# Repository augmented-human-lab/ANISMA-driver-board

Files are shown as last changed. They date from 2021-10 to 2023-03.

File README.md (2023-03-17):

[ANISMA Main Repository](https://github.com/augmented-human-lab/ANISMA) 
* [ANISMA Software](https://github.com/augmented-human-lab/ANISMA-software)
* [ANISMA Controller Board](https://github.com/augmented-human-lab/ANISMA-controller-board)
* **ANISMA Driver Board** <-- You are here!

# ANISMA Driver Board

This repository provides the Eagle Project files for the ANISMA Driver Board

The Driver Board connects to an Arduino Uno as controller board. They support eight output pins that are fully controlled and can be extended by adding more Driver Boards to an I2C bus system. We use a PCA9685 16-channel LED controller in combination with four MAX14874 dual-channel push-pull drivers in order to control the current flow using pulse-width-modulation (PWM) and dynamically set the polarity (VCC, GND, HIGH-Z) for each output pin. 

# How to get the board

Using the following link you can get direct access to the Gerber files and Bill of Materials (BOM): 
https://www.pcbway.com/project/shareproject/ANISMA_Driver_Board_3e5c784f.html

If you want you can purchase the board directly including assembly via PCBWay.

<a href="https://www.pcbway.com/project/shareproject/ANISMA_Driver_Board_3e5c784f.html">PCB from PCBWay</a>

# Wiring

Wire the ANISMA Controller Board with the Arduino Uno as follows: 

| Arduino Uno | ANISMA Controller Board | Power Supply (9V Battery) |
|---|---|---|
| SCL | SCL | |
| SDA | SDA | |
| 5V | 5V | |
| GND1 | GND | |
| GND2 | | - |
| | VSS/12V/9V | + |

anisma wiring

# Connecting your ANISMA skin deformation device to the ANISMA Driver Board
Now you can hook up your ANISMA devices to the driver board output pins. To see what pins of your ANISMA skin deformation device need to be connected to which driver board output pins, go to the Animate view in the ANISMA Software, make sure the Arduino Uno Controller Board is connected to your computer, and click "Replay with Controllerboard". Now at each node the pin number should be displayed to which to connect your device.

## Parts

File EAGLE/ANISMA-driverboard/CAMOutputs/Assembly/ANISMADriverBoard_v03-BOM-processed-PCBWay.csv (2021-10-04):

Item # | Designator | Qty | Manufacturer | Mfg Part # | Description / Value | Package/Footprint | Type | DigiKey Part | DigiKey URL | Your Instructions / Notes
1 | BUS, JPBUS | 2 | Sullins Connector Solutions | PINHD-1X5/90 |  | 1X05/90 | thru-hole | S1111E-05-ND | https://www.digikey.co.nz/en/products/detail/sullins-connector-solutions/PBC05SBAN/860345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
2 | OUT | 1 | Sullins Connector Solutions | PINHD-1X8/90 |  | 1X08/90 | thru-hole | S1111E-08-ND | https://www.digikey.co.nz/en/products/detail/sullins-connector-solutions/PBC08SBAN/860348
3 | ADR0, ADR1, ADR2, ADR3, ADR4, ADR5 | 6 |  | SJ |  | SJ | SMD |  |  | No assembly needed, please consider for pricing
4 | C2 | 1 | Walsin Technology Corporation | C-EUC0603 | 100nF | C0603 | SMD | 1292-1161-2-ND | https://www.digikey.co.nz/en/products/detail/walsin-technology-corporation/0201X104K160CT/9354659
5 | R1, R4, R5, R6, R7, R8, R9 | 7 | Stackpole Electronics Inc | 10KOHM-0603-1/10W-1% | 10k | 603 | SMD | RMCF0603FT10K0TR-ND | https://www.digikey.co.nz/en/products/detail/stackpole-electronics-inc/RMCF0603FT10K0/1761235
6 | C1 | 1 | Panasonic Electronic Components | EEE1CA470WR | EEE1CA470WR | CAP_EEE1CA470WR | SMD | PCE3890TR-ND | https://www.digikey.co.nz/en/products/detail/panasonic-electronic-components/EEE-1CA470WR/766057
7 | DRV-1, DRV-2, DRV-3, DRV-4 | 4 | Maxim Integrated | MAX14874 | MAX14874 | TD1233 | SMD | 175-MAX14874ETC+TTR-ND | https://www.digikey.co.nz/en/products/detail/maxim-integrated/MAX14874ETC-T/7392069
8 | PCA9685 | 1 | NXP USA Inc. | PCA9685PW | PCA9685PW | TSSOP28 | SMD | 568-11925-2-ND | https://www.digikey.co.nz/en/products/detail/nxp-usa-inc/PCA9685PW-118/2034325

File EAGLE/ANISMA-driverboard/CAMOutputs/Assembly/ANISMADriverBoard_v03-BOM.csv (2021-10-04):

Qty | Value | Device | Package | Parts | Description
2 |  | PINHD-1X5/90 | 1X05/90 | BUS, JPBUS | PIN HEADER
1 |  | PINHD-1X8/90 | 1X08/90 | OUT | PIN HEADER
6 |  | SJ | SJ | ADR0, ADR1, ADR2, ADR3, ADR4, ADR5 | SMD solder JUMPER
1 | 100nF | C-EUC0603 | C0603 | C2 | CAPACITOR, European symbol
7 | 10k | 10KOHM-0603-1/10W-1% | 0603 | R1, R4, R5, R6, R7, R8, R9 | 10kΩ resistor
1 | EEE1CA470WR | EEE1CA470WR | CAP_EEE1CA470WR | C1 | Check prices
4 | MAX14874 | MAX14874 | TD1233 | DRV-1, DRV-2, DRV-3, DRV-4
1 | PCA9685PW | PCA9685PW | TSSOP28 | PCA9685

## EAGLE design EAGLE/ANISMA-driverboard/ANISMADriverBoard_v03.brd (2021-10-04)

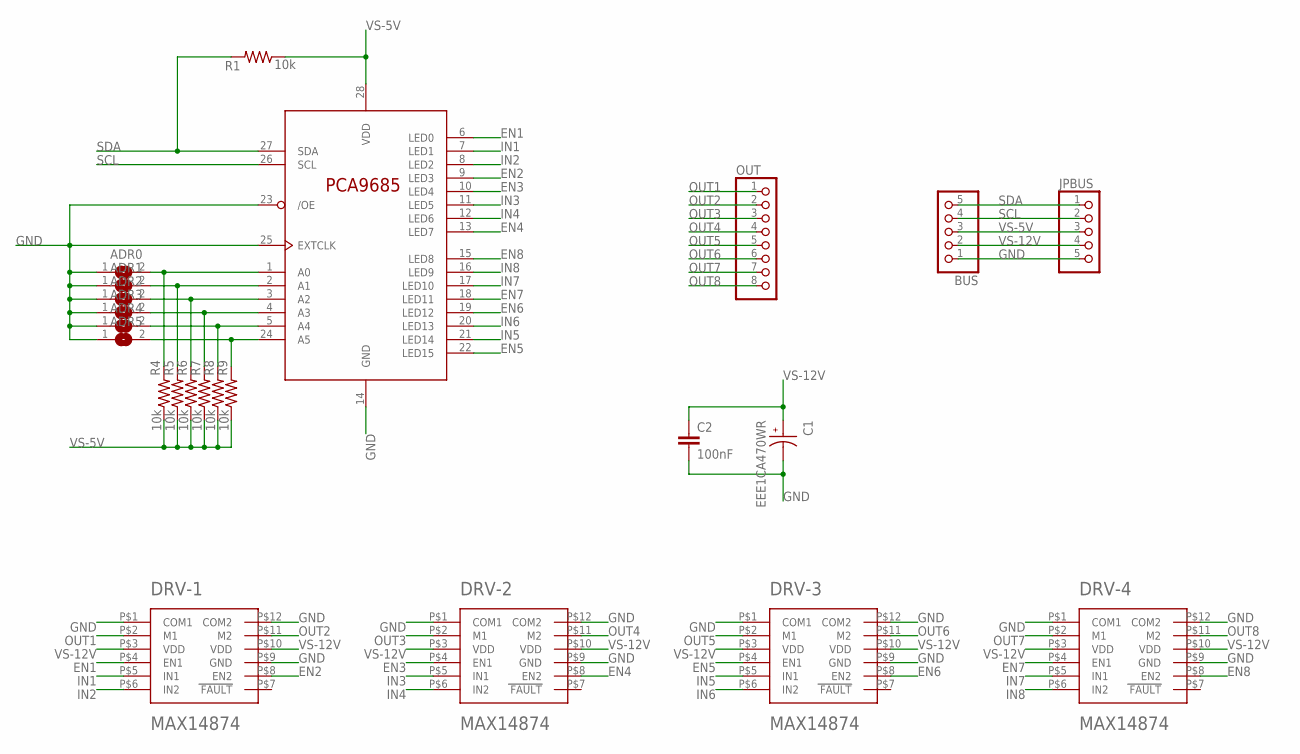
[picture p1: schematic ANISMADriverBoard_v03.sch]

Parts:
ADR0, ADR1, ADR2, ADR3, ADR4, ADR5: SJ
BUS: PINHD-1X5/90; 1X05/90
C1: EEE1CA470WR; CAP_EEE1CA470WR
C2: 100nF; C0603
DRV-1, DRV-2, DRV-3, DRV-4: MAX14874; TD1233
JPBUS: PINHD-1X5/90; 1X05/90
OUT: PINHD-1X8/90; 1X08/90
PCA9685: PCA9685PW; TSSOP28
R1, R4, R5, R6, R7, R8, R9: 10k; 0603

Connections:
EN1: DRV-1.P$4 (EN1), PCA9685.6 (LED0)
EN2: DRV-1.P$8 (EN2), PCA9685.9 (LED3)
EN3: DRV-2.P$4 (EN1), PCA9685.10 (LED4)
EN4: DRV-2.P$8 (EN2), PCA9685.13 (LED7)
EN5: DRV-3.P$4 (EN1), PCA9685.22 (LED15)
EN6: DRV-3.P$8 (EN2), PCA9685.19 (LED12)
EN7: DRV-4.P$4 (EN1), PCA9685.18 (LED11)
EN8: DRV-4.P$8 (EN2), PCA9685.15 (LED8)
GND: ADR0.1, ADR1.1, ADR2.1, ADR3.1, ADR4.1, ADR5.1, BUS.1, C1.2, C2.2, DRV-1.P$1 (COM1), DRV-1.P$9 (GND), DRV-1.P$12 (COM2), DRV-2.P$1 (COM1), DRV-2.P$9 (GND), DRV-2.P$12 (COM2), DRV-3.P$1 (COM1), DRV-3.P$9 (GND), DRV-3.P$12 (COM2), DRV-4.P$1 (COM1), DRV-4.P$9 (GND), DRV-4.P$12 (COM2), JPBUS.5, PCA9685.14 (GND), PCA9685.23 (/OE), PCA9685.25 (EXTCLK)
IN1: DRV-1.P$5 (IN1), PCA9685.7 (LED1)
IN2: DRV-1.P$6 (IN2), PCA9685.8 (LED2)
IN3: DRV-2.P$5 (IN1), PCA9685.11 (LED5)
IN4: DRV-2.P$6 (IN2), PCA9685.12 (LED6)
IN5: DRV-3.P$5 (IN1), PCA9685.21 (LED14)
IN6: DRV-3.P$6 (IN2), PCA9685.20 (LED13)
IN7: DRV-4.P$5 (IN1), PCA9685.17 (LED10)
IN8: DRV-4.P$6 (IN2), PCA9685.16 (LED9)
unnamed: ADR0.2, PCA9685.1 (A0), R4.2
unnamed: ADR1.2, PCA9685.2 (A1), R5.2
unnamed: ADR2.2, PCA9685.3 (A2), R6.2
unnamed: ADR3.2, PCA9685.4 (A3), R7.2
unnamed: ADR4.2, PCA9685.5 (A4), R8.2
unnamed: ADR5.2, PCA9685.24 (A5), R9.2
OUT1: DRV-1.P$2 (M1), OUT.1
OUT2: DRV-1.P$11 (M2), OUT.2
OUT3: DRV-2.P$2 (M1), OUT.3
OUT4: DRV-2.P$11 (M2), OUT.4
OUT5: DRV-3.P$2 (M1), OUT.5
OUT6: DRV-3.P$11 (M2), OUT.6
OUT7: DRV-4.P$2 (M1), OUT.7
OUT8: DRV-4.P$11 (M2), OUT.8
SCL: BUS.4, JPBUS.2, PCA9685.26 (SCL)
SDA: BUS.5, JPBUS.1, PCA9685.27 (SDA), R1.2
VS-5V: BUS.3, JPBUS.3, PCA9685.28 (VDD), R1.1, R4.1, R5.1, R6.1, R7.1, R8.1, R9.1
VS-12V: BUS.2, C1.1, C2.1, DRV-1.P$3 (VDD), DRV-1.P$10 (VDD), DRV-2.P$3 (VDD), DRV-2.P$10 (VDD), DRV-3.P$3 (VDD), DRV-3.P$10 (VDD), DRV-4.P$3 (VDD), DRV-4.P$10 (VDD), JPBUS.4

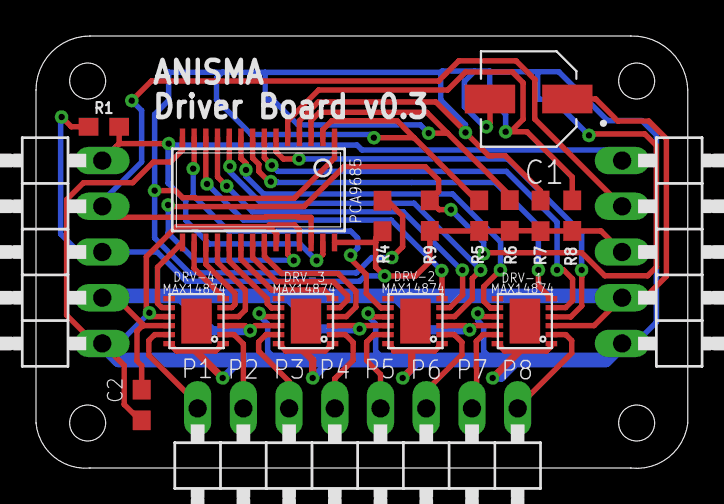
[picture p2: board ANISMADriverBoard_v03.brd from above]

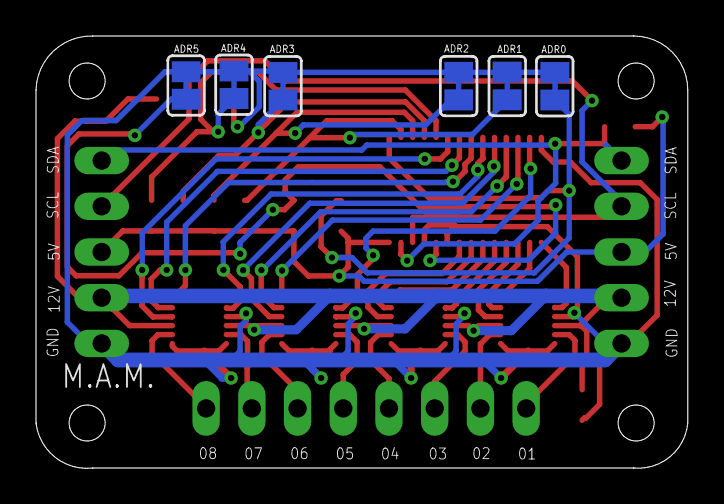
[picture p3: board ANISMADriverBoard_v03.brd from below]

Board: 2 copper layers, 36.2 x 24.0 mm, 23 parts (6 on the bottom side), 35 nets.

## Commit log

2021-10-03 added big pin labels on top layer
    [ANISMADriverBoard_v03.brd]
2021-10-04 added cam and gerber files
    [ANISMADriverBoard_v03-BOM.csv, ANISMADriverBoard_v03.brd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]
2021-10-04 adding PCBWay BOM + Centroid File
    [ANISMADriverBoard_v03-BOM-processed-PCBWay.csv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]

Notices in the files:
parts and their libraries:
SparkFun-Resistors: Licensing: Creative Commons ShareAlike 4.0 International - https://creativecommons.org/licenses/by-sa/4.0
